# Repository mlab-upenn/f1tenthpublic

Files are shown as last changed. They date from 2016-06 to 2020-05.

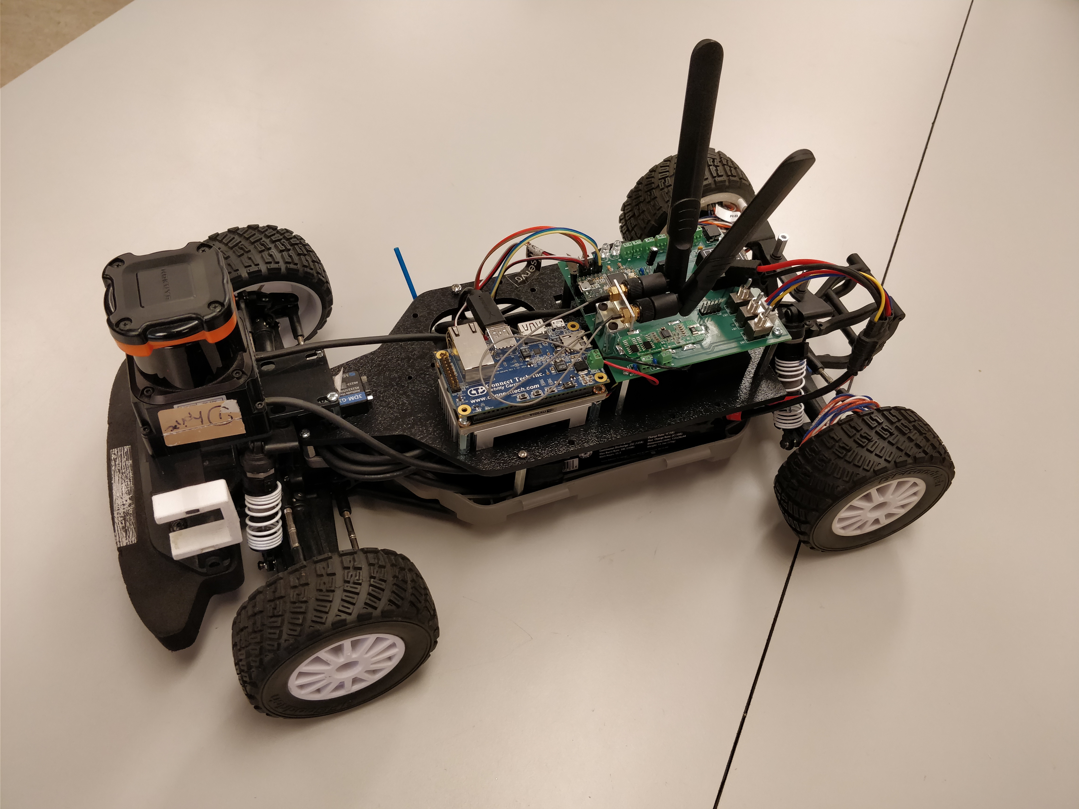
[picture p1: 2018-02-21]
images/image2.jpg

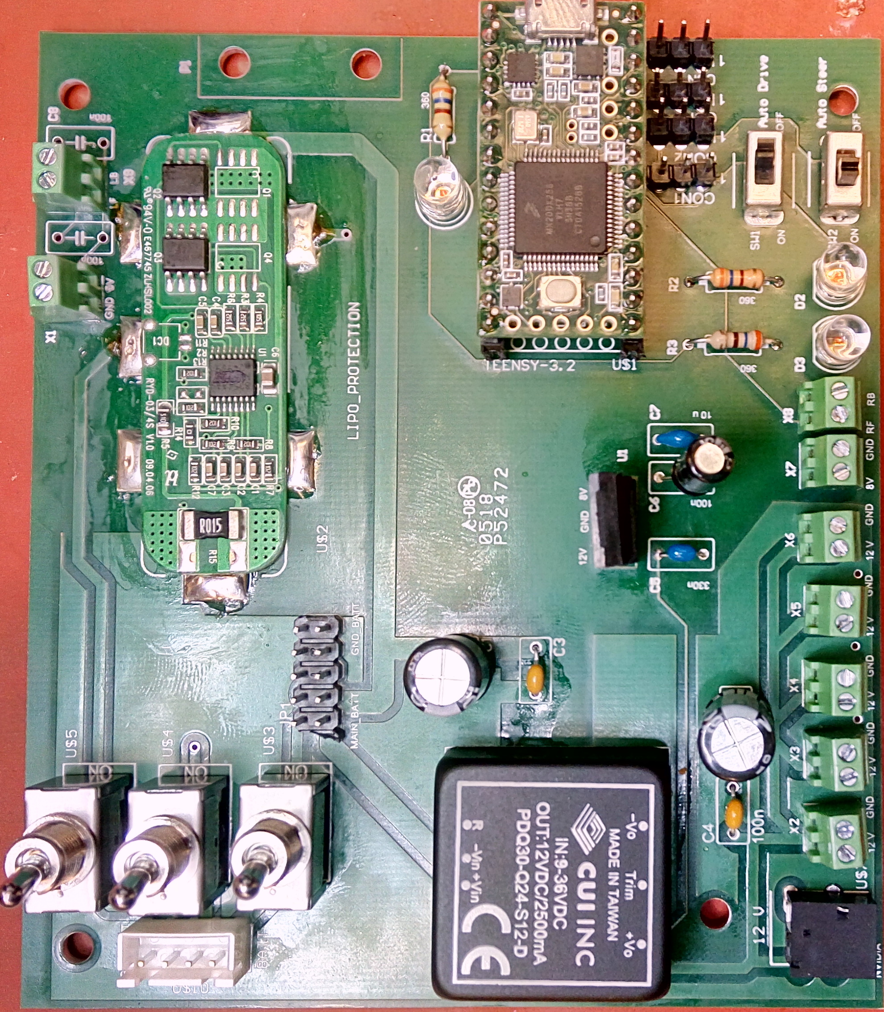
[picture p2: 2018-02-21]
images/power_board_v2.0.jpg

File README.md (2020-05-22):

# f1tenth_public, please read me
2020-05-22
This repository is no longer supported. Please see the new Build page at https://f1tenth.org/ for the most up to date BOM.

This repository hosts all of the code, CAD files, and other resources necessary to get your car ready for competition.

## F1tenth BOM 2019.xlsx
This is the bill of materials for building a F1/10 car. It contains order links for mechanical and electrical parts. The updated power board and parts list and order links are also inside.

## power-board-v3.zip
The source files of power board v3. It is designed in Altium Designer. To order the powerboard, please go to "F1tenth BOM 2019.xlsx" and find the order link in "Bill of Material for Power Board v3.0" section. The order link is https://oshpark.com/shared_projects/qvIKu3aY

### Warning: please test power board before connecting battery, Jetson and Lidar!
After soldering the power board, please test the board with a DC power supply and multimeter. 
* Using a multimeter, test if the GND_BATT pin and the opposite pin of the battery connector on the power board are shorted. Test if any 12V pin and GND pin, 8V pin and GND pin are shorted. Double check the polarity of electrolytic capacitor and the 12V to 8V DC converter. Check if the switch functions.
* Set the DC power supply to 12 V, current limit of 100 mA, and connect GND of power supply to GND_BATT pin and + of power supply to 1st pin at battery connector. Turn on power supply, and flip on the switch. Red PWR_LED should light up. Test 12V and 8V output voltage.

### Connect battery only after making sure no short circuit exists!

## Chassis
The Chassis folder contains solidworks files for making the chassis.
The following parts need to be laser cut:
* Chassis_Surfaced_MASTER_small_powerboard.DWG (for power board v3)
* Lidar_Mount_10LX.DWG or Lidar_Mount_30LX.DWG

The following parts need to be 3D printed:
* Camera_Mount.STL

The 3dPrints folder contains optional parts for zed camera.

If the FOCBOX cannot fit under the small power board, you can use only 3 standoffs to mount the power board.

## Power-board-v2.0
Old power board design source files. Obsolete. Designed in Altium Designer.

## Change log
v3:
Updated power board. Removed teensy and lithium battery charging module because no one would run the car while charging the battery.
Updated chassis to match the smaller power board.

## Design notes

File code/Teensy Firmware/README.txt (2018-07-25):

This file contains commands to setup rosserial to communicate with Teensy via ROS framework. It also involves command for generation of custom messages headers which can be accessed by code in arduino.

Setup Arduino with Teensy:

1) Setup arduino with Teensy package using link : https://www.pjrc.com/teensy/td_download.html

2) Setup rosserial : 
	Follow link : http://wiki.ros.org/rosserial_arduino/Tutorials/Arduino%20IDE%20Setup

	OR

	use commands :
	sudo apt-get install ros-indigo-rosserial-arduino
	sudo apt-get install ros-indigo-rosserial

3) To setup libraries (use custom messages):
	- go into race folder from Week 2
	- create build folder: `mkdir build`
	- move into it: `cd build`
	- run cmake on parent folder: `cmake ..`
	- now Makefile is available, so run it with: `make`
	- source created setup file: `source ./devel/setup.bash`
	- move into [place_for_arduino_projects]/libraries
	- delete old ros libs folder `rm -rf ros_lib`
	- run rosserial libraries builder `rosrun rosserial_arduino make_libraries.py .`

	Now, you should be able to find folder `race` in `ros_lib` folder with 3 header files (custom messages).

4)	Once this is configured : 
	Choose Teensy 3.2/3.1 in Tools menu of arduino software. Also make sure settings are configured to : "serial" and "96 Mhz optimized".
	After choosing the appropriate port, your arduino should be ready to dump the firmware.

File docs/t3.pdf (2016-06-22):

# Tutorial 3: The Jetson: Introduction

### The F1/10 Team

## What you should know about this board

The complete specs of the Board can be found at - Jetson Linux Homepage. (http://elinux.org/Jetson_TK1) In short, this dev board has,

- An ARM quad core Cortex-A15 CPU @ 2.3GHz
- An NVidia Kepler GK20 GPU(192 CUDA cores)
- 16GB of storage
- 2GB RAM
- Power: Takes in 12V at a current range of 1 - 5A. (Under Normal working conditions, current draw = 0.5A)
- Has optimized OpenCV libraries. Harnesses the CUDA cores for better and faster results
- The board comes up with a customised ‘Linux4Tegra’ Distribution - NVidia’s distribution of Ubuntu 14.04 with some pre-compiled binaries
There is extensive material with regard to powering on the Jetson and logging into the Desktop GUI. This NVidia (http://developer.download.nvidia.com/embedded/jetson/TK1/docs/2_GetStart/Jeston_TK1_User_Guide.pdf) guide covers the steps needed for setting up the board. There are 3 sections in that guide - ‘Setting up’ , ‘Flashing the Jetson’ and ‘Jetpack’.
We only need to go through the first section for now.
The section for ‘Flashing’ the Jetson is not required for us right now because when we boot a brand new Jetson, it already contains the Linux4Tegra files and an install script.
For developer tools related to CUDA and cross compiling resources, users can follow the 3rd section that talks about the Jetpack.
Once you switch on the Jetson, you should upgrade the kernel to ‘The Grinch Kernel’. This will enable important features needed for the race car.
Follow http://jetsonhacks.com/2015/05/26/install-grinch-kernel-for-l4t-21-3-on-nvidia-jetson-tk1/

## References

- Jetson Wiki (http://elinux.org/Jetson_TK1)
- JetsonHacks Blog Post (http://jetsonhacks.com/) (Its really good)
- NVidia Forums (https://devtalk.nvidia.com/default/board/162/)
- A Setting up Jetson Video (https://www.youtube.com/watch?v=ghqM8pzJZxg)
- Nvidia Page (https://developer.nvidia.com/embedded/jetson-development-pack)

1

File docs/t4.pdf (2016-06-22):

# Tutorial 4: Setting Up the Wireless Network

### The F1/10 Team

## Introduction

This tutorial covers the configurations required to be made on the Jetson and laptop in order to setup the point to point wireless connection between them using ubiquiti pico station.

## Setting up the Jetson’s ethernet:

Connect the Jetson to display via HDMI port. Also make sure you have a USB mouse and Keyboard connected to it.

### Physically connect the Jetson to PicoStation 2HP

- Plug in the POE (power over ethernet) injector
- Plug the PicoStation into the POE port
- Connect this system into Jetson’s LAN port

### Configure the Jetson for a static IP on the 192.168.1.x subnet

- Open network connections on Jetson
- Go to the ”wired” tab
- Edit the ethernet connection
- Go to the ”IPv4” Settings tab
- Edit the settings as follows:
– Method: Manual
– Address: 192.168.1.x (x = anynumber) (The video tutorials in further lectures will use: 192.168.1.1 to connect to Jetson via SSH. Make sure you remember the value of x you set here while following future videos.
– Netmask : 255.255.255.0
– Gateway : 192.168.1.x
– Save –> Close
- The network should say connected, you might need to select ’wired connection 1’ from the wireless toolbar and/or unplug and replug the wires

## Configuring the PicoStation

You must still be connected to the PicoStation via an ethernet connection or the PicoStation’s previously setup network (if there is one) before continuing.

### Connecting to the Pico Station

- Open a web browser and access the PicoStation’s IP address – Default IP address is 192.168.1.20
– enter http://[IP address]

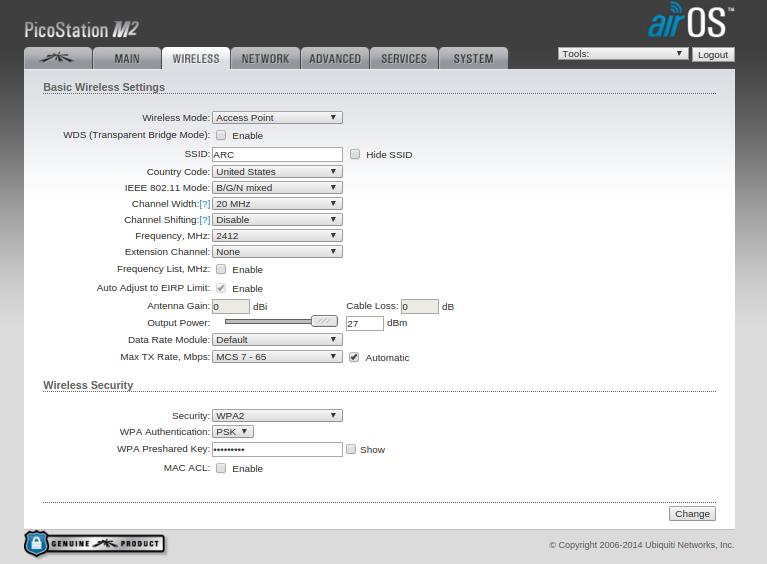
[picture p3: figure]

– Note: IP address can be changed
- Enter username and password when prompted – Default username: ubnt
– Default password: ubnt
– Note: Username and password can be changed

### Configuring the PicoStation

- Go to the ”WIRELESS” tab
- Change the settings to the following: – Wireless Mode: Access Point – SSID: [desired SSID]
* example: My network
– Country Code: United States
– IEEE 208.11 Mode: B/G/N mixed – Channel Spectrum Width: 20 MHz – Channel Shifting: Disabled
– Channel: 1-2412 MHz
– Output Power: no greater than 27 dBm (U.S. regulation) – Data Rate Module: Default
– Security: WPA2
– WPA Authentication : PSK
– WPA Preshared Key : Your Password

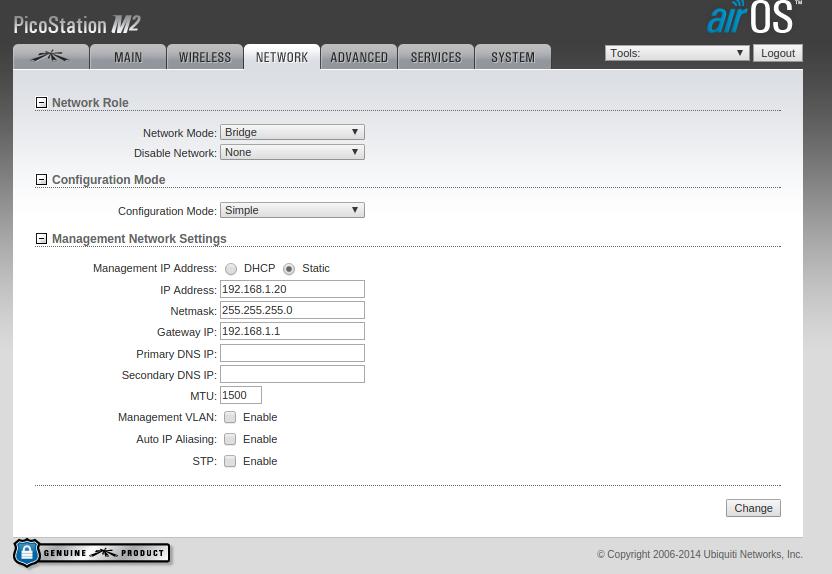
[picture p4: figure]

- Go to the ”NETWORK” tab
- Change the settings to the following: – Network Mode: Bridge
– Disable Network: None
– Bridge IP Address: Static – IP Address: 192.168.1.20 – Netmask: 255.255.255.0
– Gateway IP: 192.168.1.1
– Change –> Apply

## Setting up the Remote System’s Wireless

### Setting up the wireless

- Go back to your Network Connections
- Go to the ”Wireless” tab
- Add a new wireless connection
– Name it after the intended robot
– Give it the same SSID that you gave the PicoStation – Go to ”IPv4 Settings” tab
– Change the settings as follows:
* Method: Manual
* Address: 192.168.1.x (x=any number, 110 in our case for future examples) * Netmask: 255.255.255.0
* Gateway: 192.168.1.x (x=any number, 110 in our case)

– Save –> Close

### Connecting via SSH

Now once you are connected to the wireless network, you can ssh into the Jetson from your remote system’s terminal, using following command:

ssh ubuntu@192 . 1 6 8 . 1 . 1

Here ”ubuntu” is the username setup in Jetson and the ip shown is the IP configured in the first step in setting up of pico station.

## Establishing ROS over network

In order to let ROS communicate directly between you Jetson and remote system, and send messages to and fro, it requires a few minor configurations. While operating Jetson via remote system, you might need to see the data published over certain topics by scripts running on Jetson. You might need to visualize the location of the car, or the LiDAR scans or maybe the map of the surrounding. A GUI called Rviz allows this visuals but we cannot install that on Jetson. Establishing ROS to communicate over the network, will allow us to use this GUI to visualize data in this way. We will cover this visualization in the next tutorial.
To set this up, follow the steps below:
- On the terminal of remote system, when present working directory is the home folder, open ”.bashrc” using any text editor.
- Add the lines :

export ROS_MASTER_URI=http ://192.168.1.1:11311 export ROS_IP=192.168.1.110

- Whenever you want to revert this, replace it back by :

export ROS_HOSTNAME=localhost
export ROS_MASTER_URI=http :// localhost :11311
- Open the hosts file under path : /etc/, and add the line :

192.168.1.1 ubuntu

Here it is assumed that the ”ubuntu” is the account username in Jetson, and 192.168.1.1 is the IP address to which the wireless was setup on Jetson.

Now on the Jetson Side:
- Open the file .bashrc from home folder.
- Add the following line when you want to transfer data to remote system over network

export ROS_IP=192.168.1.1

- To revert it back to original settings, replace above line with :

export ROS_HOSTNAME=localhost
export ROS_MASTER_URI=http :// localhost :11311

- Now navigate to the ”/etc/hosts” file and add the following line to it: (The username refers to the username of your laptop. And the IP mentioned corresponding to the IP you used while setting up the remote system/laptop’s wireless.

192.168.1.110 username

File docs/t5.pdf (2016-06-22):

# Tutorial 5: Sensor Configuration and Rosbags

### The F1/10 Team

## Introduction

This tutorial will cover the installation of various packages and settings to be configured to get the LiDAR and Inertial Measurement Unit working on Jetson. At the end we will go through few commands that can be used to record the data to run them later on for simulations.

## Transcript to the Video Tutorial

In this video we will install and configure the Hokuyu LiDAR and Razor IMU. Luckily both have of these have ROS packages readily available and hence the process is quite straight forward. For any other sensor you might want to use in future, you can look up to its package availability in ROS and follow similar steps.

Connect your jetson board to display, keyboard, mouse and an ethernet cable.

On the terminal use the following command to install the Hokuyu node package:

sudo apt−get i n s t a l l ros−indigo−hokuyu−node

When you connect your lidar to jetson, it generally connects to ACM ports which can be checked using the command :

l s /dev/ttyACM*

This will list all the ACM ports currently being used. If you are doing this first time, you need to provide specific permissions to the port by using the command :

sudo chmod a+rw /dev/ttyACM_

This will provide read write permissions for ROS to communicate with the sensor. Now, to check the data coming from LiDAR, as explained in the initial ROS tutorials, run the roscore. On the other terminal , run -rostopic list. This will show all the topics currently being published.

The scan topic is the one we are interested in.

rostopic echo /scan

These dump of messsages might not make sense now, but these values correspond to the distance sensed by LiDAR at different angles.

We can visualize these laser scans by a GUI interface called Rviz. Unfortunately due to the driver issues Rviz doesn’t work on Jetson. If you had setup ROS over Network explained in previous tutorial properly, you can run Rviz over your system that has been setup for the network.

AS you can see these are the laser scans. It might not show up on its own on your system. Insert it using the add button visible here.

Now to install the packages for IMU, go back to Jetson and install the package using command :

sudo apt−get i n s t a l l ros−indigo−razor−imu−9dof

Lets keep the default parameters untouched, and take a copy for us to make some tweaks

roscd razor_imu_9dof/ config cp razor . yaml my_razor . yaml

You can calibrate the IMU by following the link provided in the reference. and mention the measured offset values in the newly made file. To confirm the communication of IMU with ROS interface use the launch file:

roslaunch razor_imu_9dof razor−pub . launch

You can now run ”rostopic list” in another window and look for the /imu topic. ”rostopic echo /imu” will allow you to see the incoming data stream. So the packages for both these sensors are ready. You can follow similar steps to install it on any ROS system. Its better not to clog Jetson’s memory with useless packages and hence you install any extra packages on your laptop.

For example to visualize the IMU data, you need to install the python-visual package. Install the IMU packages on your ROS system as well. Then install the python- visual using :

sudo apt−get i n s t a l l python−visual

Once done, run the launch file :

roslaunch razor_imu_9dof razor−pub−and−display . launch

The red board is following the motion of my IMU. Feel free to change the config parameters and play around with this to improve the performance.

## Introduction to Rosbags

This tutorial covers data logging tools provided by the Robot Operating System. These tools allow users to capture data from various sensors and then play it back offline. This tutorial goes over some basic commands to utilise these logging tools. This should be ideally read after you go through the Sensor Integration Video.

## Rosbags: Tutorial 5.1

In this tutorial we are going to learn about rosbags. You would now know how dependant we are on the various sensors for testing and running our algorithms. The problem arises when we don’t always have access to these sensors. rosbag is the tool provided by ROS that lets us log sensor data and play it back as per our need.
It stores this sensor data as the topics on which it was published and when the data is played back, its published again on those same topics. Therefore the remaining part of our system need not change when we need to test anything ofline.

You could go ahead and download the files located at https://github.com/mlab-upenn/f1_10_code_public/
- Git Repo

In a terminal after initialising roscore run this command,

$ rosbag play lidarBag . bag − −clock

This .bag file contains the data from our LIDAR. After this command, on another terminal, use rostopic list to verify that you are able to see the /scan topic. This is the topic that the LIDAR was publishing on when it was actually used. The clock arguement here is a very important paramter. It provides a simulated ‘clock’ for the ROS network. The data playing back from the bags would have time stamps highly offset from the current time. This discrepency in time between the incoming data and the rest of the system often leads to unpredictable and generally unwanted behaviour. For this reason, the ’clock’ is used - It provides all the ROS systems with a common time stamp - a simulated time stamp. If you perform a rostopic list in a terminal, you will see the /clock topic that is being published. The other subsystems of your ROS framework need to be told that they must follow the simulated time and not actual time. To do this we must set the ros parameter use_sim_time to true. To do this, run the following command on a terminal

$ rosparam set use_sim_time

To check the value of the paramter use,

$ rosparam get use_sim_time

Ensure this configuration of use_sim_time every time you playback a bag.
Now we will go through the process of actually taking recording a bag. Lets use the Hokuyo and the IMU as our sensors. Launch the sensors using,

$ rosrun hokuyo_node hokuyo_node $ roslaunch razor imu_launch

For bagging all current topics, use the -a command line argument with the command

$ rosbag record −a

You can choose to terminate the bagging process at any time by simply killing that process - Ctrl + C should do it.
You will notice now that you will have a bag in your current folder. Use

$ rosbag <bag name>.bag info

to view the contents of the bag. This data can be then played with the command shown earlier to simulate the LIDAR data ofline.
Hopefully you guys understood the need and usefullness of the bagging process. This tutorial like the others was a very concise version of the Official tutorials on the ROS Wiki. Please visit [1] for more commands and options regarding the rosbag tool.

## References

[1] http://wiki.ros.org/rosbag - Rosbags Wiki
[2] Calibrating the Inertial Measurement Unit : Section 7 in http://wiki.ros.org/razor_imu_9dof

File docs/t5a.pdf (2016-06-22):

# Extras: Configuring the Hokuyo UST 10LX

### The F1/10 Team

## Introduction

This tutorial covers setting up the UST 10LX LIDAR in regard to its network configuration. (You will need access to a windows system with administrator rights for completing this tutorial)

## LIDAR Setup

The LIDAR communicates with the jetson through the Ethernet to USB converter and this connection shows up on the Jetson as a new ethernet connection. Use ‘ifconfig’ in the terminal to verify this.

$ i f c o n c f i g

There are now two ethernet connections on the Jetson - one for the ubiquiti and the other for the LIDAR. To make sure we can communicate between these two we have to ensure that they are on the same subnet. Lets start with the default values of the IP for the LIDAR. View the datasheet for the particulars [1].
For this particular tutorial the following ip addresses are used

# gateway of ubiquti network − 192.168.1.1

# eth1 ( ubiquiti network ) on jetson − 192.168.1.5

# eth2 (LIDAR connection ) on jetson − 192.168.0.10 − Default values

- STEP 1: Lets first manually assign the correct IP address to the LIDAR. On the windows system download the URG data viewing tool and the IP changing tool - [2], [3].
Manually assign an ip address to the ethernet network connection of the Windows PC with these values:

IP Address 192.168.0.15
Subnet Mask 255.255.255.0
Default Gateway 192.168.0.1

Once you donwload these tools, connect the LIDAR to the Windows machine - Use the Benri data viewing tool to verify that your machine has detected the LIDAR and that you can see the data(Fig. 1).

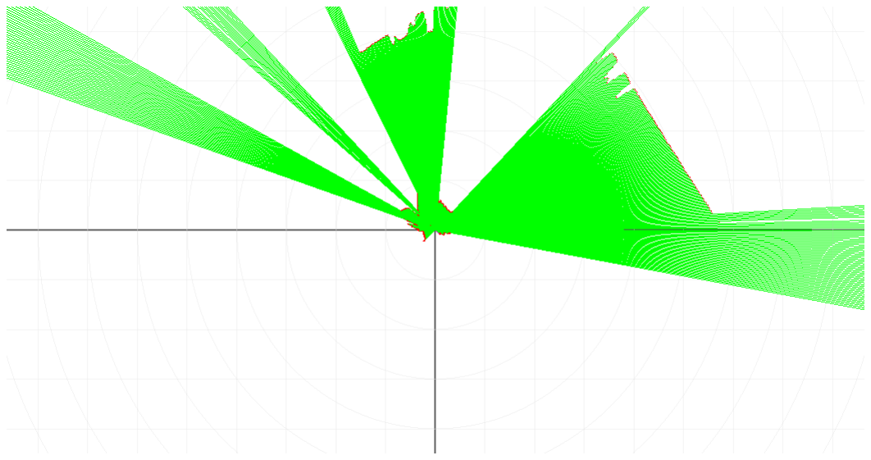
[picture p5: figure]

Figure 1: Data as seen on the UrgBenri Data viewing tool

Now, use the ip changing tool to assign the following values to the LIDAR.

IP Address 192.168.1.11
Subnet Mask 255.255.255.0
Gateway 192.168.1.1

Once the dialog box says the ip is ‘Updated’, disconnect the device from the machine. Change the ethernet ip of the

machine to

IP Address 192.168.1.15
Subnet Mask 255.255.255.0
Default Gateway 192.168.1.1

Plug in the LIDAR back into the system and make sure you can see visualize the data on the URGBenri tool.
- STEP 2: We will now configure the network setup on the Jetson. Create a new ethernet connection in linux4Tegra[4] with these values

Connection Name: Hokuyo
IP Address 192.168.1.15
Subnet Mask 255.255.255.0
Default Gateway 192.168.1.1

Once you make this new connection, you should be able to plug in the LIDAR and the ubiquiti and be able to connect to both these devices, i.e, ‘ifconfig’ should display two ethernet connections - eth0 and eth1 with the correct IPs’ for each. (If you were connected to the ubiquiti network through your own systems, you might notice that you get disconnected from the network the moment you connect the LIDAR to the Jetson. We will address this issue in the next step)
- STEP 3: We will now setup a bridge network that allows the 2 ethernet connections on the Jetson to coexist. First, install bridge-utils on the Jetson.

$ sudo apt−get i n s t a l l bridge−u t i l s

Once installed follow the enter the listed commands into the terminal(on the Jetson)

1. sudo brctl addbr br0
2. sudo brctl addif br0 eth1
3. sudo brctl addif br0 eth2
4. sudo i f c o n f i g br0 192.168.1.2 netmask 255.255.255.0 up

(*Note: make sure you already don’t have some existing connection on 192.168.1.2 - If thats the case, just set the bridge network to any other available IP on 192.168.1.xx) After this step, you should be able to see br0 listed as a connection under when you do ifconfig.
- STEP 4: You should now be able to connect back to the ubiquiti network from your systems. Use nmap[5] to see the different devices connected on your network. In the terminal, type

$ nmap −sP 192.168.1.0/24

You should be able to view the host names with the IPs of all the devices sharing your network. You must be able to spot the LIDAR and the Jetson as separate devices on this list.
- STEP 5: Once you see the devices listed with nmap, you should be able to ssh into the Jetson and run

$ rosrun urg_node urg_node _ip_address :=192.168.1.11

(Note: You should have the urg node package installed when you need to run this node)

$ sudo apt−get i n s t a l l ros−indigo−urg−node

This should start broadcasting the /scan topic. From your personal computer, make sure you can echo this topic. You are all set now to use the LIDAR over network.

## References

[1] UST 10LX datasheet (http://en.manu-systems.com/ust-10lx_spec_E.pdf)

[2] URG DataViewing Tools (https://www.hokuyo-aut.jp/02sensor/07scanner/download/data/UrgBenri.htm)
[3] URG IP changing tool (https://www.hokuyo-aut.jp/02sensor/07scanner/download/data/Urg_ip_changer_utm_en.zip)
[4] Create new ethernet connection (https://help.ubuntu.com/16.04/ubuntu-help/net-manual.html)
[5] nmap Tool (https://nmap.org/)

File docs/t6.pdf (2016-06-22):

# Tutorial 6: Distance finder and PID

### The F1/10 Team

## Introduction

This article contains the transcript of the week 2 Video Tutorial 6: Distance finder and PID. The aim of this tutorial is to give a brief explanation of simple algorithm to maintain the car parallel in a corridor. It involves how to use the sensor data from lidar and how to formulate a controller for the same.

## Transcript of Video Tutorial

In this tutorial we will learn how to make our car run parallel to a wall at a fixed distance. We will implement two nodes, a node that uses the laser scans from the lidar to determine the distance from the wall and an other node to apply pid on this error to determine the steering angle. We shall follow the algorithm described in the lectures.
Lets go through a simple procedure to calculate the distance of the wall from the car and hence calculate the deviation from the desired trajectory. The lidar scans from right to left corresponding to 0 to 180 degree with 90 degree being the front of the car. We pick 2 rays at 0 degree and theta degree, theta being some angle between 0 to 70 degree.

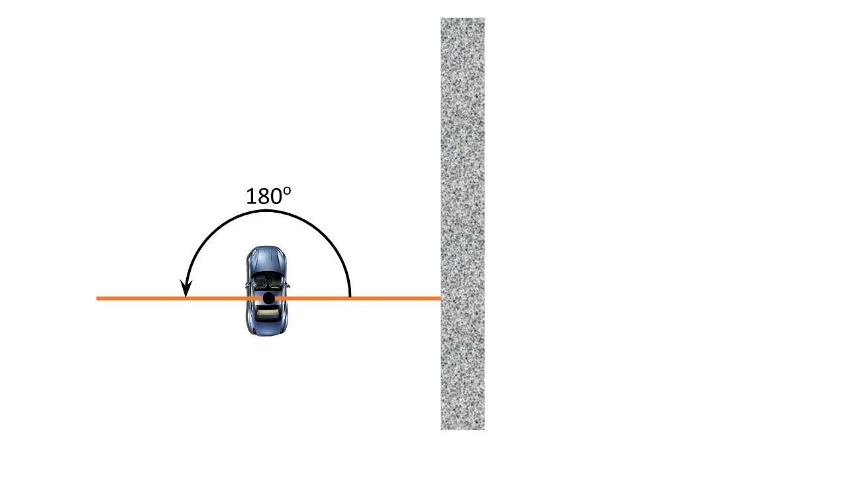
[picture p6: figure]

Figure 1: Lidar scan angles

Let alpha be the orientation of the car with respect to the wall. By solving the geometric problem we can establish alpha as tan inverse of a cos(theta) - b/asin(theta), and AB as b cos(alpha).

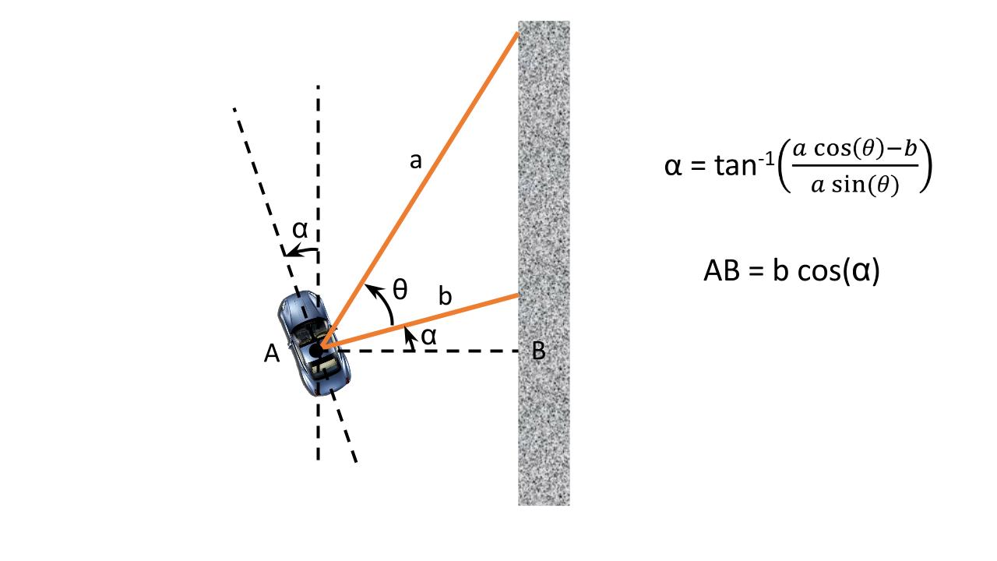
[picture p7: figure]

Figure 2: Calculating the orientation and distance from the wall

1

If the desired trajectory is 1m from the wall then generally the error that has to controlled by the PID is 1
- AB.
But we cannot use this distance directly. Due to the high speed of the car and a finite delay in execution of the manoeuvre we project the car forward certain distance from its current position. Hence now the distance of the car from the wall becomes AB + AC*sin(alpha)
Hence the error to be compensated for is the difference between CD and the desired trajectory.
Now we have the error, we can use it in the PID equation to determine the amount of correction to be given to the steering.

Figure 3: Projecting the car future in time

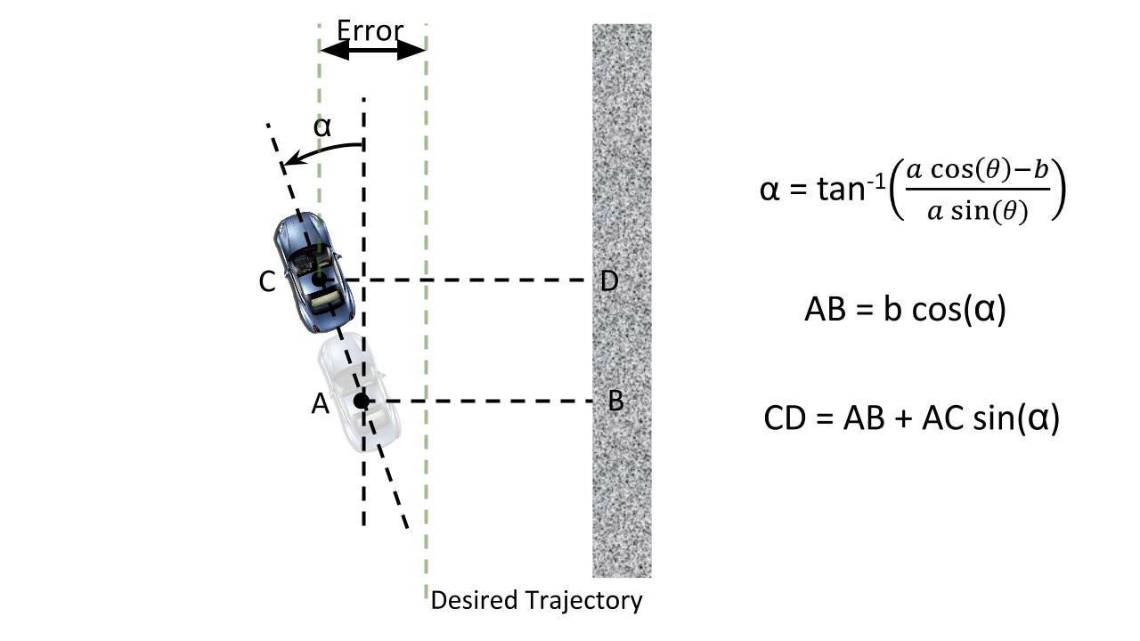
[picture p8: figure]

We use the standard PID[1] equation, where e(t) is the error from the desired trajectory. As seen in the lecture we will be using only Kp and Kd controls.
Hence we implement this as a tunable variable Kp times error plus another tunable variable Kd times the difference in error.

Vθ = Kp × e(t) + Kd

de(t)
dt
Vθ = Kp × error + Kd × previous error - current error

Use this value to increment or decrement your your steering angle. In the practice session you will be implementing this in code.

## References

[1] A simple PID tutorial (http://www.csimn.com/CSI_pages/PIDforDummies.html)

2

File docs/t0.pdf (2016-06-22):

# Tutorial 0: The Robot Operating System

### The F1/10 Team

## Installing ROS Indigo on Ubuntu 14.04

This tutorial assumes that the host OS on which ROS Indigo is to be installed is Ubuntu 14.04 LTS. This tutorial offers a very concise walkthrough of the ROS Installation. For a detailed step-by-step explaination of the commands used, please visit the ROS Inidgo Installation page . (http://wiki.ros.org/indigo/Installation/Ubuntu)
If you have the Trusty 14.04.2(use lsb_release -a in the terminal to find out) distribution, you might face dependancy issues for which it is recommended you vist the link above before begginig the install. The steps listed below install the ‘Desktop-Full’ ROS Indigo. This means that simluators like Gazebo, rViz along with a large number of ROS packages are installted as well. If your host machine has any constraints regarding memory you should visit the link above to install a trimmed version of ROS Indigo.
Again, this is a very brief guide and if there is any problem at any step please visit the link above.
Execute the following commands/steps in the terminal one after the other.
- Configre Ubuntu repositories to allow for ‘multiverse’, ‘universe’ and ‘restricted’. (How to : Configure Repositories) (https://help.ubuntu.com/community/Repositories/Ubuntu)
- sudo sh -c ‘echo “deb http://packages.ros.org/ros/ubuntu $(lsb_release -sc) main” > /etc/opt/sources.list.d/ros-latestlist’
- sudo apt-key adv –keyserver hkp://pool.sks-keyservers.net –recv-key 0xB01FA116
- sudo apt-get update
- sudo apt-get install ros-indigo-desktop-full
- sudo rosdep init
- rosdep update
- echo “source /opt/ros/indigo/setup.bash” >> ∼/.bashrc
- source ∼/.bashrc
- sudo apt-get install python-rosinstall
You should now have ROS Indigo on your system.

## References

- ROS Indigo Installation (http://wiki.ros.org/indigo/Installation/Ubuntu)

1

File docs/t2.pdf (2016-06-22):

# Tutorial 2: The Robot Operating System: Basics 2

### The F1/10 Team

## Introduction

This article contains the transcript of the Video Tutorial 2: The Basics of ROS (Part 2). This tutorial is based on tutorial 12 covered by the official ROS tutorials[1]. The aim of this tutorial is to familiarize you with the framework of the Robot Operating System by implementing your own simple publisher and subscriber nodes in python.

## Transcript of Video Tutorial

In this tutorial lets write our own publisher node that publishes a string hello world and a subscriber node that receives the string. We begin by creating a workspace. In your root folder, execute these commands:

$ mkdir −p ~/catkin_ws/ src $ cd ~/catkin_ws/ src
$ catkin_init_workspace

Catkin[2] is a ROS tool for compiling the different subsystems and modules used in ROS. Its like CMake, but over a larger scale and its specially designed keeping in mind some ROS requirements. Perform a catkin_make from the root of the workspace.

$ cd . .
$ catkin_make

The devel and build folders at the root of the workspace are where the linked libraries and the complied code in machine language resides. Source the environment using

$ source devel/setup . bash

We will now create a package. In the src folder,type in the command

$ catkin_create_pkg beginner_tutorials std_msgs rospy roscpp

The beginner_tutorials is the name of the package and the std_msgs, rospy, roscpp are dependencies that we are defining. Use catkin_make from the root of the workspace. Source and confirm if your workspace is indeed added to your current environment by doing

$ echo ROS_PACKAGE_PATH

We will now use the roscd command to access a package within a workspace. If the environment containing the package is sourced, we should be able to naviagte to the pacakge by using roscd package name. here we can verify this by using

$ roscd beginner t u t o r i a l s

We will create a new folder to hold all our code

$ mkdir s c r i p t s
$ cd s c r i p t s

Place the talker.py and listener.py files in the script folder just created.
Lets walk through the talker.py file first
- ‘from std_msgs.msg import String’ line imports the string data type from the std_msgs library that we included during the creation of beginner_tutorials package
- The rospy.Publisher function creates a new topic called chatter of type string
- rospy.init_node initializes the node called talker, and
- pub.publish(hello_str) publishes the string containing hello world with the system time. The listener.py consists of a similar structure.
- Like in the talker node rospy.init_node intializes the listener node.
- But this node subscribes to the chatter topic published by the talker node using the rospy.Subscriber function
- The callback function is an interrupt function that is called every time some data is published to the chatter topic. Here we just print back the string that it received.
Before we can run the nodes we need to give executable permissions to these files using

$ sudo chmod +x talker . py l i s t e n e r . py

To build the nodes navigate to the root of the workspace and run

$ cd ~/catkin_ws
$ catkin_make

make sure the process ends without errors Start roscore,

$ roscore

then in new terminals run the talker.py and listener.py nodes. Make sure you source the workspace using

$ source ~/catkin_ws/devel/setup . bash

every time you open a new terminal. Run the nodes using

$ rosrun beginner_tutorials l i s t e n e r . py

and in a seperate terminal

$ source ~/catkin_ws/devel/setup . bash $ rosrun beginner_tutorials talker . py

Go ahead and run all the rosnode, rostopic, rosmsg and rqt_graph commands to analyze the program. In the next tutorial you will learn how to configure and run ROS on the jetson.

## References

[1] ROS Beginner Tutorial 12 (http://wiki.ros.org/ROS/Tutorials/WritingPublisherSubscriber%28python%29)
[2] What exactly is catkin (http://wiki.ros.org/catkin)

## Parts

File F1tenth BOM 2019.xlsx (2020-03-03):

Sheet: v3.0
Component | Quantity | Cost |  | Link | Order Status | Comment
Traxxas 1/10th Car platform with RC, NiMH battery 3000mAh, 7 cell and Charger | 1 | $299.95 | $299.95 | http://www.jegs.com/i/Traxxas/430/74054-6/10002/-1 | 0 | If out of stock, see alternate platforms below
USB wifi dongle |  | $8.99 | $0.00 | http://amzn.to/2nQGg3Z | 0 | use onboard WLAN or usb dongles like these instead of Ubiquity picostation ( product is discontinued)
Li-Po battery 5000mAh, 3 cell 11.1V #2872 | 1 | $74.99 | $74.99 | https://traxxas.com/products/parts/batteries/idpowercellbatteries/lipo/2872X-5000mah-111v-3S-25C | 0 | Combinations also available for purchase : https://www.amazon.com/dp/B01M0PKSGB https://www.amazon.com/Traxxas-Maxx-Brushless-BATTERY-CHARGER/dp/B00ERUAQYO
 |  |  |  | https://www.amazon.com/Traxxas-2831X-5000mAh-3-Cell-Battery/dp/B01A6YDKS8
Li-Po battery Charger #2970 | 1 | $49.99 | $49.99 | https://traxxas.com/products/parts/chargers/2970ezpeakplus4ampid https://www.amazon.com/Traxxas-2970-EZ-Peak-Charger-Identification/dp/B00OAFYLJC https://traxxas.com/products/parts/chargers/ezpeak-dual-8amp-id | 0
Nvidia Jetson TX1 | 1 | $299.00 | $299.00 | https://www.nvidia.com/en-us/autonomous-machines/embedded-systems-dev-kits-modules/ http://www.nvidia.com/object/edu-discount.html http://www.nvidia.com/object/jetsontx2-edu-discount.html | 0 | Avail Tx1/TX2 Development Kit through Academic discount Also, either of TX1 or TX2 can be used
Orbitty Carrier board for TX1 | 1 | $173.00 | $173.00 | http://connecttech.com/product/orbitty-carrier-for-nvidia-jetson-tx2-tx1/ | 0 | works for both TX1 or TX2
USB Hub | 1 | $29.95 | $29.95 | https://www.amazon.com/AmazonBasics-Port-USB-Power-Adapter/dp/B00DQFGH80 https://www.amazon.com/Sabrent-4-Port-Individual-Switches-HB-UM43/dp/B00JX1ZS5O | 0
FTDI | 1 | $15.00 | $15.00 | https://www.sparkfun.com/products/9873 | 0 | optional - depending on the IMU module
Sensors
SparkFun 9DoF Razor IMU M0 | 1 | $49.95 | $49.95 | https://www.sparkfun.com/products/14001 | 0
3DM Microstrain IMU (optional) |  |  |  | http://www.microstrain.com/inertial/3dm-gx3-25 |  | use either IMU
UM7 IMU (optional) |  |  |  | https://www.pololu.com/product/2740 http://www.chrobotics.com/shop/um7-orientation-sensor
LIDAR | 1 | $1775.00 | $1775.00 | https://acroname.com/products/HOKUYO-UST-10LX-LASER?sku=R359-UST-10LX | 0 | or scan-sweep lidar
Structure Sensor (Optional) | 1 | $379.00 | $379.00 | https://store.structure.io/store | 0 | or sviz - lidar and camera bundle
Asus xtion pro (optional) |  | - | - | https://www.amazon.com/Asus-Xtion-PRO-LIVE-90IW0122-B01UA/dp/B00CET0ZBO https://www.newegg.com/Product/Product.aspx?Item=N82E16826785030 |  | out of stock mostly
ZED Camera (Optional) |  | $449.00 | $0.00 | https://www.stereolabs.com/ | 0 | or rgb option
Mechanical
Traxxas 3769 Spring Preload Spacers | 2 | $5.22 | $10.44 | http://amzn.to/2aazUF7 | 0
Allen Key Set | 1 | $8.99 | $8.99 | http://amzn.to/29PazD5 | 0
Camera mount - 3d printed | 2 |  |  | - |  | 3d printed from files provided
Ubiquity Picostation mount - 3d printed ( optional) | 1 |  |  | - |  | 3d printed from files provided
plastic spacers /standoffs | 4 |  |  |  |  | between the carrier board and the TX1 mounting
3mm ABS | 1 | $6.38 | $6.38 | http://amzn.to/29E6CTy https://www.mcmaster.com/#8586k361/=1bnvvd6 | 0 | For Lidar mount of chassis
6mm ABS | 1 | $9.74 | $9.74 | http://amzn.to/29PayPj https://www.mcmaster.com/#8586k371/=1bnvv5e | 0 | For Base plate of chassis
6mm Hex M/F Standoff 14mm | 8 | 4.2 | $33.60 | https://www.mcmaster.com/#93655a425/=1bhcvt6
6mm Hex F/F Standoff 19mm | 6 | 2.79 | $16.74 | https://www.mcmaster.com/#92080a430/=1ak2153
6mm Hex F/F Standoff 45 mm | 4 | 2.8 | $11.20 | https://www.mcmaster.com/#92080a030/=1ak1644
6mm Hex F/F Standoff 35 mm | 4 | 2.53 | $10.12 | https://www.mcmaster.com/#92080a024/=1ak1tj1
M3 screws x 10 mm | 26 | 7.01 | $7.01 | https://www.mcmaster.com/#91290a115/=1bhcq40 |  | for a pack of 100
M3 screws x 20 mm | 6 | 6.85 | $6.85 | https://www.mcmaster.com/#91502a109/=1bhcs7r |  | for a pack of 50
Power Board
Refer to the Power Board BOM for specific components
Miscelleneous
Traxxas 2976 AC to DC Converter | 1 | $25.79 | $25.79 | http://amzn.to/29Fx5xq | 0
Micro USB Cable | 1 | $4.99 | $4.99 | http://amzn.to/29xNHFc | 0 | for teensy to usb hub
Ethernet cable (optional) | 1 | $2.99 | $2.99 | http://amzn.to/29xO2ry | 0 | for ubiquity (optional)
POE cable (optional) | 1 | $3.99 | $3.99 | http://amzn.to/29D7Lou | 0 | for ubiquity (optional)
Traxxas Lipo to JST balance cable extender | 1 | $14.99 | $14.99 | https://www.amazon.com/HobbyStar-Traxxas-Charge-Adapter-Adapters/dp/B076N68H4G https://www.amazon.com/dp/B071GS515J/ref=psdc_2234135011_t1_B075W3C42B
USB to Ethernet adapter ( for lidar with ethernet conn) | 1 | $9.49 | $9.49 | https://www.amazon.com/Cable-Matters-Ethernet-Network-Adapter/dp/B00ET4KHJ2
Servo cable | 1 | $3.00 | $3.00 | http://amzn.to/29xPaeq | 0 | ($3.06 per pack of 10)
4 AA batteries | 1 | $7.18 | $7.18 | http://amzn.to/29EIImY | 0 | for RC
SD Cards (optional) | 2 | $24.95 | $49.90 | http://amzn.to/29ItJe7 | 0
Bill of Material for Power Board v4.0
Revised by Kim Luong (kimluong@seas.upenn.edu) 2019-09-05 10:47AM EST
Comment | Quantity | Cost |  | Components |  | Comment | Order Link | Comments | Digikey Part Number
Power Board | 1 | $30.00 | $30.00 |  |  | Comes in packs of 3 | https://tinyurl.com/f110powerboard2019
560 ohm | 1 | $0.04 | $0.04 | R1 |  | Resistor |  | Any resistor around 500 ohm should work | ‎CF14JT560RCT-ND‎ (https://www.digikey.com/product-detail/en/CF14JT560R/CF14JT560RCT-ND/1830344/?itemSeq=302805132)
0.33uF | 1 | $0.45 | $0.45 | C5 |  | CAPACITOR, American symbol |  |  | ‎445-181227-1-ND‎ (https://www.digikey.com/product-detail/en/FG16X7R2A334KNT06/445-181227-1-ND/9740707/?itemSeq=302805131)
0.1uF | 3 | $0.23 | $0.69 | C6, C3, C4 |  | CAPACITOR, American symbol |  |  | BC1084CT-ND
100uF | 2 | $0.31 | $0.62 | C1, C2 |  | CAPACITOR, American symbol |  |  | ‎P5182-ND‎ (https://www.digikey.com/product-detail/en/ECA-1HM101/P5182-ND/245041/?itemSeq=302805123)
10uF | 1 | $0.23 | $0.23 | C7 |  | CAPACITOR, American symbol |  |  | 493-5915-1-ND‎ (https://www.digikey.com/product-detail/en/UVR1H100MDD1TD/493-5915-1-ND/3438479/?itemSeq=302805129)
12V to 8V LDO | 1 | $0.86 | $0.86 | U1 |  | 12V to 8V LDO |  |  | BA7808CP-E2CT-ND‎ (https://www.digikey.com/product-detail/en/BA7808CP-E2/BA7808CP-E2CT-ND/2357332/?itemSeq=302805130)
12V_TRANSFORMER | 1 | $34.94 | $34.94 | U$9 |  | CUI Inc ?? SERIES: PDQ30-D ?? DESCRIPTION: DC-DC CONVERTER http://www.mouser.com/pdfdocs/pdq30-d.pdf |  |  | ‎102-3892-ND‎ (https://www.digikey.com/product-detail/en/PDQ30-Q24-S12-D/102-3892-ND/6165425/?itemSeq=302805124)
2 Pin Terminal Blocks | 7 | $0.91 | $6.37 | X1, X2, X3, X4, X5, X6, X7 |  | .100 (2.54mm) Center Header - 2 Pin" |  |  | ‎ED10561-ND‎ (https://www.digikey.com/product-detail/en/OSTVN02A150/ED10561-ND/1588862/?itemSeq=302805120)
Toggle Switch | 1 | $4.51 | $4.51 | U$3 |  | SPST two lead switch Pin 2 is common Swtich Closed on Down Position DigiKey: http://www.digikey.com/product-detail/en/nkk-switches/M2011S2A1W01/360-3240-ND/1049342 Data Sheet: http://2t70un3m1d9z1kztamkdrd38.wpengine.netdna-cdn.com/wp-content/uploads/2016/02/MtogglesBushing.pdf |  |  | ‎360-3240-ND‎ (https://www.digikey.com/product-detail/en/M2011S2A1W01/360-3240-ND/1049342/?itemSeq=302805119)
antenna pads | 1 |  | $0.00 | P1 |  |  | From Nvidia dev board |  | Antenna pads
4 Pin Connector | 1 | $0.21 | $0.21 | U$10 |  |  |  |  | 455-2249-ND‎ (https://www.digikey.com/product-detail/en/B4B-XH-A(LF)(SN)/455-2249-ND/1651047/?itemSeq=302805122)
Power LED | 1 | $0.58 | $0.58 | LED 1 |  | LED power indicator |  | Or any other 5mm LED, current around 20 mA | LED5MM
 |  | Total | $3468.72

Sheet: v2.0
Component | Quantity | Cost |  | Link | Order Status | Comment
Traxxas 1/10th Car platform with RC, NiMH battery 3000mAh, 7 cell and Charger | 1 | $299.95 | $299.95 | http://www.jegs.com/i/Traxxas/430/74054-6/10002/-1 | 0 | If out of stock, see alternate platforms below
USB wifi dongle |  | $8.99 | $0.00 | http://amzn.to/2nQGg3Z | 0 | use onboard WLAN or usb dongles like these instead of Ubiquity picostation ( product is discontinued)
Li-Po battery 5000mAh, 3 cell 11.1V #2872 | 1 | $74.99 | $74.99 | https://traxxas.com/products/parts/batteries/idpowercellbatteries/lipo/2872X-5000mah-111v-3S-25C | 0 | Combinations also available for purchase : https://www.amazon.com/dp/B01M0PKSGB https://www.amazon.com/Traxxas-Maxx-Brushless-BATTERY-CHARGER/dp/B00ERUAQYO
 |  |  |  | https://www.amazon.com/Traxxas-2831X-5000mAh-3-Cell-Battery/dp/B01A6YDKS8
Li-Po battery Charger #2970 | 1 | $49.99 | $49.99 | https://traxxas.com/products/parts/chargers/2970ezpeakplus4ampid https://www.amazon.com/Traxxas-2970-EZ-Peak-Charger-Identification/dp/B00OAFYLJC https://traxxas.com/products/parts/chargers/ezpeak-dual-8amp-id | 0
Nvidia Jetson TX1 | 1 | $299.00 | $299.00 | https://www.nvidia.com/en-us/autonomous-machines/embedded-systems-dev-kits-modules/ http://www.nvidia.com/object/edu-discount.html http://www.nvidia.com/object/jetsontx2-edu-discount.html | 0 | Avail Tx1/TX2 Development Kit through Academic discount Also, either of TX1 or TX2 can be used
Orbitty Carrier board for TX1 | 1 | $173.00 | $173.00 | http://connecttech.com/product/orbitty-carrier-for-nvidia-jetson-tx2-tx1/ | 0 | works for both TX1 or TX2
USB Hub | 1 | $29.95 | $29.95 | https://www.amazon.com/AmazonBasics-Port-USB-Power-Adapter/dp/B00DQFGH80 https://www.amazon.com/Sabrent-4-Port-Individual-Switches-HB-UM43/dp/B00JX1ZS5O | 0
FTDI | 1 | $15.00 | $15.00 | https://www.sparkfun.com/products/9873 | 0 | optional - depending on the IMU module
Sensors
SparkFun 9DoF Razor IMU M0 | 1 | $49.95 | $49.95 | https://www.sparkfun.com/products/14001 | 0
3DM Microstrain IMU (optional) |  |  |  | http://www.microstrain.com/inertial/3dm-gx3-25 |  | use either IMU
UM7 IMU (optional) |  |  |  | https://www.pololu.com/product/2740 http://www.chrobotics.com/shop/um7-orientation-sensor
LIDAR | 1 | $1775.00 | $1775.00 | https://acroname.com/products/HOKUYO-UST-10LX-LASER?sku=R359-UST-10LX | 0 | or scan-sweep lidar
Structure Sensor (Optional) | 1 | $379.00 | $379.00 | https://store.structure.io/store | 0 | or sviz - lidar and camera bundle
Asus xtion pro (optional) |  | - | - | https://www.amazon.com/Asus-Xtion-PRO-LIVE-90IW0122-B01UA/dp/B00CET0ZBO https://www.newegg.com/Product/Product.aspx?Item=N82E16826785030 |  | out of stock mostly
ZED Camera (Optional) |  | $449.00 | $0.00 | https://www.stereolabs.com/ | 0 | or rgb option
Mechanical
Traxxas 3769 Spring Preload Spacers | 2 | $5.22 | $10.44 | http://amzn.to/2aazUF7 | 0
Allen Key Set | 1 | $8.99 | $8.99 | http://amzn.to/29PazD5 | 0
Camera mount - 3d printed | 2 |  |  | - |  | 3d printed from files provided
Ubiquity Picostation mount - 3d printed ( optional) | 1 |  |  | - |  | 3d printed from files provided
plastic spacers /standoffs | 4 |  |  |  |  | between the carrier board and the TX1 mounting
3mm ABS | 1 | $6.38 | $6.38 | http://amzn.to/29E6CTy https://www.mcmaster.com/#8586k361/=1bnvvd6 | 0 | For Lidar mount of chassis
6mm ABS | 1 | $9.74 | $9.74 | http://amzn.to/29PayPj https://www.mcmaster.com/#8586k371/=1bnvv5e | 0 | For Base plate of chassis
6mm Hex M/F Standoff 14mm | 8 | 4.2 | $33.60 | https://www.mcmaster.com/#93655a425/=1bhcvt6
6mm Hex F/F Standoff 19mm | 6 | 2.79 | $16.74 | https://www.mcmaster.com/#92080a430/=1ak2153
6mm Hex F/F Standoff 45 mm | 4 | 2.8 | $11.20 | https://www.mcmaster.com/#92080a030/=1ak1644
6mm Hex F/F Standoff 35 mm | 4 | 2.53 | $10.12 | https://www.mcmaster.com/#92080a024/=1ak1tj1
M3 screws x 10 mm | 26 | 7.01 | $7.01 | https://www.mcmaster.com/#91290a115/=1bhcq40 |  | for a pack of 100
M3 screws x 20 mm | 6 | 6.85 | $6.85 | https://www.mcmaster.com/#91502a109/=1bhcs7r |  | for a pack of 50
Power Board
Refer to the Power Board BOM for specific components
Miscelleneous
Traxxas 2976 AC to DC Converter | 1 | $25.79 | $25.79 | http://amzn.to/29Fx5xq | 0
Micro USB Cable | 1 | $4.99 | $4.99 | http://amzn.to/29xNHFc | 0 | for teensy to usb hub
Ethernet cable (optional) | 1 | $2.99 | $2.99 | http://amzn.to/29xO2ry | 0 | for ubiquity (optional)
POE cable (optional) | 1 | $3.99 | $3.99 | http://amzn.to/29D7Lou | 0 | for ubiquity (optional)
Traxxas Lipo to JST balance cable extender | 1 | $14.99 | $14.99 | https://www.amazon.com/HobbyStar-Traxxas-Charge-Adapter-Adapters/dp/B076N68H4G https://www.amazon.com/dp/B071GS515J/ref=psdc_2234135011_t1_B075W3C42B
USB to Ethernet adapter ( for lidar with ethernet conn) | 1 | $9.49 | $9.49 | https://www.amazon.com/Cable-Matters-Ethernet-Network-Adapter/dp/B00ET4KHJ2
Servo cable | 1 | $3.00 | $3.00 | http://amzn.to/29xPaeq | 0 | ($3.06 per pack of 10)
4 AA batteries | 1 | $7.18 | $7.18 | http://amzn.to/29EIImY | 0 | for RC
SD Cards (optional) | 2 | $24.95 | $49.90 | http://amzn.to/29ItJe7 | 0
Bill of Material for Power Board v3.0
On 2/5/2019 at 11:41:38 AM
Comment | Quantity | Cost |  | Components |  | Comment | Order Link | Comments | Pattern
Power Board | 1 | 30 | 30 |  |  |  | https://oshpark.com/shared_projects/PM1kJ6E3
560 ohm | 1 |  | 0 | R1 |  | Resistor | https://www.digikey.com/product-detail/en/stackpole-electronics-inc/CF14JT560R/CF14JT560RTR-ND/1741466 | Any resistor around 500 ohm should work | AXIAL-0.4
0.33uF | 1 |  | 0 | C5 |  | CAPACITOR, American symbol | https://www.digikey.com/product-detail/en/tdk-corporation/FK16X7R2A334K/445-8365-ND/2815295 |  | C050-035X075
100nF | 3 |  | 0 | C6, C3, C4 |  | CAPACITOR, American symbol | https://www.digikey.com/product-detail/en/kemet/C328C102K3G5TA7301/C328C102K3G5TA7301-ND/6671502 |  | C050-035X075 | For a bag of capacitors (except the 0.33 u): | https://www.sparkfun.com/products/13698
100u | 2 |  | 0 | C1, C2 |  | CAPACITOR, American symbol | https://www.digikey.com/product-detail/en/panasonic-electronic-components/ECA-1HM101B/P10397TB-ND/268482 |  | C050-035X075
10uF | 1 |  | 0 | C7 |  | CAPACITOR, American symbol | https://www.digikey.com/product-detail/en/nichicon/UVR1H100MDD1TD/493-5915-1-ND/3438479 |  | C050-035X075
12V to 8V LDO | 1 | 0.92 | 0.92 | U1 |  | 12V to 8V LDO | https://www.digikey.com/product-detail/en/rohm-semiconductor/BA7808CP-E2/BA7808CP-E2CT-ND/2357332 |  | BA7808CP-E2
12V_TRANSFORMER | 1 | 34.94 | 34.94 | U$9 |  | CUI Inc ?? SERIES: PDQ30-D ?? DESCRIPTION: DC-DC CONVERTER http://www.mouser.com/pdfdocs/pdq30-d.pdf | https://www.digikey.com/product-detail/en/cui-inc/PDQ30-Q24-S12-D/102-3892-ND/6165425 |  | 12V_TRANSFORMER
22-23-2021 | 7 | 0.94 | 6.58 | X1, X2, X3, X4, X5, X6, X7 |  | .100 (2.54mm) Center Header - 2 Pin" | https://www.digikey.com/product-detail/en/on-shore-technology-inc./ostvn02a150/ed10561-nd/1588862 |  | 22-23-2021
360-3240-ND | 1 | 3.37 | 3.37 | U$3 |  | SPST two lead switch Pin 2 is common Swtich Closed on Down Position DigiKey: http://www.digikey.com/product-detail/en/nkk-switches/M2011S2A1W01/360-3240-ND/1049342 Data Sheet: http://2t70un3m1d9z1kztamkdrd38.wpengine.netdna-cdn.com/wp-content/uploads/2016/02/MtogglesBushing.pdf | https://www.digikey.com/product-detail/en/nkk-switches/M2011S2A1W01/360-3240-ND/1049342 |  | 360-3240-ND
antenna pads | 1 |  | 0 | P1 |  |  | From Nvidia dev board |  | Antenna pads
BATT | 1 | 0.21 | 0.21 | U$10 |  |  | https://www.digikey.com/products/en?keywords=b4b-xh-a(LF)(SN) |  | BATTERY_CONNECTOR
Power LED | 1 | 0.41 | 0.41 | LED 1 |  | LED power indicator | https://www.digikey.com/product-detail/en/lite-on-inc/LTL-4263/160-1964-ND/3198540 | Or any other 5mm LED, current around 20 mA | LED5MM | For a bag of 25 red LED | https://www.sparkfun.com/products/9856
 |  | Total | $3465.65

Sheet: v1.0
Component | Quantity | Cost |  | Link | Order Status | Comment
Traxxas 1/10th Car platform with RC, NiMH battery 3000mAh, 7 cell and Charger | 1 | $299.95 | $299.95 | http://www.jegs.com/i/Traxxas/430/74054-6/10002/-1 | 0 | If out of stock, see alternate platforms below
Ubiquity Picostation | 1 | $0.00 | $0.00 | http://amzn.to/29QPlq8 | 0 | Phased out of production. Use USB wifi dongles like one suggested below
Energizer Battery Pack | 1 | $159.00 | $159.00 | http://amzn.to/2aaBmHu | 0 | This replaces the older XP8000, which is no longer available
Nvidia Jetson TK1 | 1 | $192.99 | $192.99 | http://amzn.to/29EI3C2 | 0
USB Hub | 1 | $29.95 | $29.95 | http://amzn.to/29D7kKG | 0
FTDI | 1 | $15.00 | $15.00 | https://www.sparkfun.com/products/9873 | 0
Sensors
SparkFun 9DoF Razor IMU M0 | 1 | $49.95 | $49.95 | https://www.sparkfun.com/products/14001 | 0
LIDAR | 1 | $1775.00 | $1775.00 | https://acroname.com/products/HOKUYO-UST-10LX-LASER?sku=R359-UST-10LX | 0
Structure Sensor (Optional) | 1 | $379.00 | $379.00 | https://store.structure.io/store | 0
ZED Camera (Optional) | 1 | $449.00 | $449.00 | https://www.stereolabs.com/ | 0
Mechanical
Traxxas 3769 Spring Preload Spacers | 2 | $5.22 | $10.44 | http://amzn.to/2aazUF7 | 0
Allen Key Set | 1 | $8.99 | $8.99 | http://amzn.to/29PazD5 | 0
3mm ABS | 1 | $6.38 | $6.38 | http://amzn.to/29E6CTy | 0
6mm ABS | 1 | $9.74 | $9.74 | http://amzn.to/29PayPj | 0
M3 Hex nuts | 1 | $2.06 | $2.06 | http://www.mcmaster.com/#90591a250/=139rn2d | 0 | ($2.06 per pack of 100)
M3 Screw x 8mm | 1 | $6.58 | $6.58 | http://www.mcmaster.com/#91290A113 | 0 | ($6.58 per pack of 100)
M1.6 Screw x 8mm | 1 | $3.01 | $3.01 | http://www.mcmaster.com/#91290a041/=139r25l | 0 | ($3.01 per pack of 25)
M3 M-F Hex Standoff x 14mm | 12 | $1.57 | $18.84 | http://www.mcmaster.com/#98952a037/=139rm51 | 0
Power Board
Teensy 3.1 | 1 | $19.80 | $19.80 | https://www.pjrc.com/store/teensy32.html | 0
Miscelleneous
Traxxas 2976 AC to DC Converter | 1 | $25.79 | $25.79 | http://amzn.to/29Fx5xq | 0
Micro USB Cable | 1 | $4.99 | $4.99 | http://amzn.to/29xNHFc | 0
Mini USB Cable | 2 | $4.99 | $9.98 | https://www.amazon.com/Rerii-Length-Angle-cable-Charging/dp/B01E6MZBG0?s=wireless | 0
Ethernet cable | 1 | $2.99 | $2.99 | http://amzn.to/29xO2ry | 0
POE cable | 1 | $3.99 | $3.99 | http://amzn.to/29D7Lou | 0
Servo cable | 1 | $3.00 | $3.00 | http://amzn.to/29xPaeq | 0 | ($3.06 per pack of 10)
4 AA batteries | 1 | $7.18 | $7.18 | http://amzn.to/29EIImY | 0
Barrel Jack Connectors | 1 | $5.36 | $5.36 | http://amzn.to/29xOnKT | 0
M-M DC power coupler | 1 | $6.99 | $6.99 | http://amzn.to/2aaBvLn | 0
SD Cards | 2 | $24.95 | $49.90 | http://amzn.to/29ItJe7 | 0
 |  | Total | $3555.85

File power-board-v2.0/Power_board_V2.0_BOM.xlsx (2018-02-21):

S.No. | Designator | Description | Part No | Comment | Footprint | Quantity | Order link
1 | C1, C2 | 100uF polarized throughole capacitor |  | 100u | C050-035X075 | 2
2 | C3, C4, C6, C8, C9 | 100nF non-polarized throughole capacitor |  | 100n | C050-035X075 | 5
3 | C5 | 330nF non-polarized throughole capacitor |  | 0.33uF | C050-035X075 | 1
5 | C7 | 10uF polarized throughole capacitor |  | 10uF | C050-035X075 | 1
6 | CON1, CON2, CON3, CON4 | 3x1 0.1" male headers |  | 3 pin male header | MA03-1 | 4
7 | D2, D3, LED1 | Red colour throughole Led |  | Led | LED5MM | 3
8 | JP1 | 5x2 0.1" male headers |  | 2x5 male headers | 2X05 | 1
9 | P1 | Right angled Antenna bracket with screws and ufl to SMA cable along with Antennas |  | Antenna bracket | Antenna pads | 1 | Extract from Nvidia TX1 dev board | https://www.ebay.com/itm/ipx-u-fl-to-sma-Male-MHF4-MALE-FEMALE-Antenna-Extension-Cable-MINI-PCI-Card/192116656446
10 | R2, R3, R1 | 360 ohm throughole resistors |  | 360ohms | 0207/10 | 3
11 | SWITCH1, SWITCH2 | SWITCH SLIDE SPDT 100MA 12V | OS102011MS2QN1 | CKN9565-NDCKN9565-ND | CKN9565-ND | 2 | https://www.digikey.com/products/en?keywords=CKN9565-ND
12 | U1 | IC REG LINEAR 8V 1A TO220CP-3 | BA7808CP-E2 | 12V to 8V LDO | BA7808CP-E2 | 1 | https://www.digikey.com/product-detail/en/rohm-semiconductor/BA7808CP-E2/BA7808CP-E2CT-ND/2357332
13 | U$1 | Teensy 3.2 microcontroller with male pins |  | TEENSY-3.2 | TEENSY-3.2 | 1 | https://www.pjrc.com/store/teensy32_pins.html
14 | U$2 | 3S LiPo Protection PCB | Tenergy protection module | LIPO_PROTECTION | LIPO_PROTECTION | 1 | https://www.amazon.com/gp/product/B0021ZN8WY
15 | U$3, U$4, U$5 | SWITCH TOGGLE SPST 6A 125V | M2011S2A1W01 | 360-3240-ND | 360-3240-ND | 3 | https://www.digikey.com/product-detail/en/nkk-switches/M2011S2A1W01/360-3240-ND/1049342
16 | U$7 | CONN PWR JACK 1.7X4MM SOLDER | PJ-054 | 12 V connector for nvidia |  | 1 | https://www.digikey.com/product-detail/en/cui-inc/PJ-054/CP-054-ND/1644595 https://www.digikey.com/product-detail/en/cui-inc/PJ-018H-SMT-TR/CP-018HPJCT-ND/1530984
17 | U$9 | DC/DC CONVERTER 12V 30W | PDQ30-Q24-S12-D | 12V_TRANSFORMER | 12V_TRANSFORMER | 1 | https://www.digikey.com/product-detail/en/cui-inc/PDQ30-Q24-S12-D/102-3892-ND/6165425
18 | U$10 | CONN HEADER XH TOP 4POS 2.5MM | B4B-XH-A(LF)(SN) | BATT | BATTERY_CONNECTOR | 1 | https://www.digikey.com/products/en?keywords=b4b-xh-a(LF)(SN)
19 | X1, X2, X3, X4, X5, X6, X7, X8, X9 | CONN TERM BLOCK 2.54MM 2POS PCB | OSTVN02A150 | 22-23-2021 | 22-23-2021 | 9 | https://www.digikey.com/product-detail/en/on-shore-technology-inc./ostvn02a150/ed10561-nd/1588862
20 |  | 14x1 0.1" Female header (for Teensy on the PCB) |  |  |  | 2
21 |  | M3 screws x 10 mm |  | For mounting the Antenna Brackets |  | 2 | https://www.mcmaster.com/#91290a115/=1bhcq40
22 |  | 6mm Hex F/F Standoff 19mm |  |  |  | 2 | https://www.mcmaster.com/#92080a430/=1ak2153

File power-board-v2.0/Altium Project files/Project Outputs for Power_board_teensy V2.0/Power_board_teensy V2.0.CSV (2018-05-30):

Bill of Material for
On 1/31/2018 at 2:59:21 PM
Comment | Pattern | Quantity | Components
0.33uF | C050-035X075 | 1 | C5 | CAPACITOR, American symbol
1 | MA03-1 | 1 | CON1 | PIN HEADER
100n | C050-035X075 | 2 | C3, C4 | CAPACITOR, American symbol
100nF | C050-035X075 | 3 | C6, C8, C9 | CAPACITOR, American symbol
100u | C050-035X075 | 2 | C1, C2 | CAPACITOR, American symbol
10uF | C050-035X075 | 1 | C7 | CAPACITOR, American symbol
12 V | CP-054-ND | 1 | U$7 | DigiKey: http://www.digikey.com/product-detail/en/cui-inc/PJ-054/CP-054-ND/1644595 Data Sheet: http://www.cui.com/product/resource/pj-054.pdf
12V to 8V LDO | BA7808CP-E2 | 1 | U1 | 12V to 8V LDO
12V_TRANSFORMER | 12V_TRANSFORMER | 1 | U$9 | CUI Inc ¦ SERIES: PDQ30-D ¦ DESCRIPTION: DC-DC CONVERTER http://www.mouser.com/pdfdocs/pdq30-d.pdf
2.2v 20mA | LED5MM | 1 | LED1 | LED OSRAM: - CHIPLED LG R971, LG N971, LY N971, LG Q971, LY Q971, LO R971, LY R971 LH N974, LH R974 LS Q976, LO Q976, LY Q976 LO Q996 - Hyper CHIPLED LW Q18S LB Q993, LB Q99A, LB R99A - SideLED LS A670, LO A670, LY A670, LG A670, LP A670 LB A673, LV A673, LT A673, LW A673 LH A674 LY A675 LS A676, LA A676, LO A676, LY A676, LW A676 LS A679, LY A679, LG A679 - Hyper Micro SIDELED® LS Y876, LA Y876, LO Y876, LY Y876 LT Y87S - SmartLED LW L88C, LW L88S LB L89C, LB L89S, LG L890 LS L89K, LO L89K, LY L89K LS L896, LA L896, LO L896, LY L896 - TOPLED LS T670, LO T670, LY T670, LG T670, LP T670 LSG T670, LSP T670, LSY T670, LOP T670, LYG T670 LG T671, LOG T671, LSG T671 LB T673, LV T673, LT T673, LW T673 LH T674 LS T676, LA T676, LO T676, LY T676, LB T676, LH T676, LSB T676, LW T676 LB T67C, LV T67C, LT T67C, LS T67K, LO T67K, LY T67K, LW E67C LS E67B, LA E67B, LO E67B, LY E67B, LB E67C, LV E67C, LT E67C LW T67C LS T679, LY T679, LG T679 LS T770, LO T770, LY T770, LG T770, LP T770 LB T773, LV T773, LT T773, LW T773 LH T774 LS E675, LA E675, LY E675, LS T675 LS T776, LA T776, LO T776, LY T776, LB T776 LHGB T686 LT T68C, LB T68C - Hyper Mini TOPLED® LB M676 - Mini TOPLED Santana® LG M470 LS M47K, LO M47K, LY M47K Source: http://www.osram.convergy.de LUXEON: - LUMILED® LXK2-PW12-R00, LXK2-PW12-S00, LXK2-PW14-U00, LXK2-PW14-V00 LXK2-PM12-R00, LXK2-PM12-S00, LXK2-PM14-U00 LXK2-PE12-Q00, LXK2-PE12-R00, LXK2-PE12-S00, LXK2-PE14-T00, LXK2-PE14-U00 LXK2-PB12-K00, LXK2-PB12-L00, LXK2-PB12-M00, LXK2-PB14-N00, LXK2-PB14-P00, 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
2 | MA03-1 | 1 | CON2 | PIN HEADER
22-23-2021 | 22-23-2021 | 9 | X1, X2, X3, X4, X5, X6, X7, X8, X9 | .100 (2.54mm) Center Header - 2 Pin"
3.3v 10mA | LED5MM | 2 | D2, D3 | LED OSRAM: - CHIPLED LG R971, LG N971, LY N971, LG Q971, LY Q971, LO R971, LY R971 LH N974, LH R974 LS Q976, LO Q976, LY Q976 LO Q996 - Hyper CHIPLED LW Q18S LB Q993, LB Q99A, LB R99A - SideLED LS A670, LO A670, LY A670, LG A670, LP A670 LB A673, LV A673, LT A673, LW A673 LH A674 LY A675 LS A676, LA A676, LO A676, LY A676, LW A676 LS A679, LY A679, LG A679 - Hyper Micro SIDELED® LS Y876, LA Y876, LO Y876, LY Y876 LT Y87S - SmartLED LW L88C, LW L88S LB L89C, LB L89S, LG L890 LS L89K, LO L89K, LY L89K LS L896, LA L896, LO L896, LY L896 - TOPLED LS T670, LO T670, LY T670, LG T670, LP T670 LSG T670, LSP T670, LSY T670, LOP T670, LYG T670 LG T671, LOG T671, LSG T671 LB T673, LV T673, LT T673, LW T673 LH T674 LS T676, LA T676, LO T676, LY T676, LB T676, LH T676, LSB T676, LW T676 LB T67C, LV T67C, LT T67C, LS T67K, LO T67K, LY T67K, LW E67C LS E67B, LA E67B, LO E67B, LY E67B, LB E67C, LV E67C, LT E67C LW T67C LS T679, LY T679, LG T679 LS T770, LO T770, LY T770, LG T770, LP T770 LB T773, LV T773, LT T773, LW T773 LH T774 LS E675, LA E675, LY E675, LS T675 LS T776, LA T776, LO T776, LY T776, LB T776 LHGB T686 LT T68C, LB T68C - Hyper Mini TOPLED® LB M676 - Mini TOPLED Santana® LG M470 LS M47K, LO M47K, LY M47K Source: http://www.osram.convergy.de LUXEON: - LUMILED® LXK2-PW12-R00, LXK2-PW12-S00, LXK2-PW14-U00, LXK2-PW14-V00 LXK2-PM12-R00, LXK2-PM12-S00, LXK2-PM14-U00 LXK2-PE12-Q00, LXK2-PE12-R00, LXK2-PE12-S00, LXK2-PE14-T00, LXK2-PE14-U00 LXK2-PB12-K00, LXK2-PB12-L00, LXK2-PB12-M00, LXK2-PB14-N00, LXK2-PB14-P00, 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
3 | MA03-1 | 1 | CON3 | PIN HEADER
360-3240-ND | 360-3240-ND | 3 | U$3, U$4, U$5 | SPST two lead switch Pin 2 is common Swtich Closed on Down Position DigiKey: http://www.digikey.com/product-detail/en/nkk-switches/M2011S2A1W01/360-3240-ND/1049342 Data Sheet: http://2t70un3m1d9z1kztamkdrd38.wpengine.netdna-cdn.com/wp-content/uploads/2016/02/MtogglesBushing.pdf
360ohms | 0207/10 | 2 | R2, R3 | RESISTOR, European symbol
4 | MA03-1 | 1 | CON4 | PIN HEADER
70ohms | 0207/10 | 1 | R1 | RESISTOR, European symbol
AGND |  | 1 | AGND2 | SUPPLY SYMBOL
antenna pads | Antenna pads | 1 | P1
BATT | BATTERY_CONNECTOR | 1 | U$10
CKN9565-NDCKN9565-ND | CKN9565-ND | 2 | SWITCH1, SWITCH2
GND_12 |  | 2 | AGND1, AGND3 | SUPPLY SYMBOL
LIPO_PROTECTION | LIPO_PROTECTION | 1 | U$2
PINHD-2X5 | 2X05 | 1 | JP1 | PIN HEADER
TEENSY-3.2 | TEENSY-3.2 | 1 | U$1 | 0.1 pin spacing"
V11.2 |  | 1 | V1 | SUPPLY SYMBOL
V12 |  | 7 | VDD1, VDD5, VDD6, VDD7, VDD8, VDD9, VDD10 | SUPPLY SYMBOL
V8 |  | 3 | VDD2, VDD3, VDD4 | SUPPLY SYMBOL

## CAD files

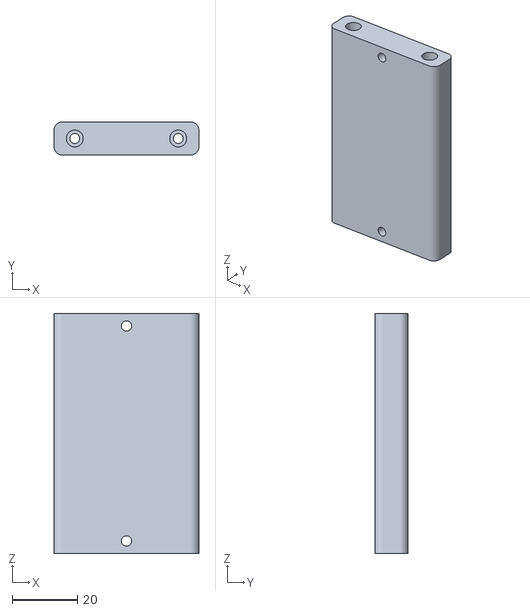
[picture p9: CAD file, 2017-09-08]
chassis/3dPrints/WifiMount.STL
44.5 x 10.2 x 73.7

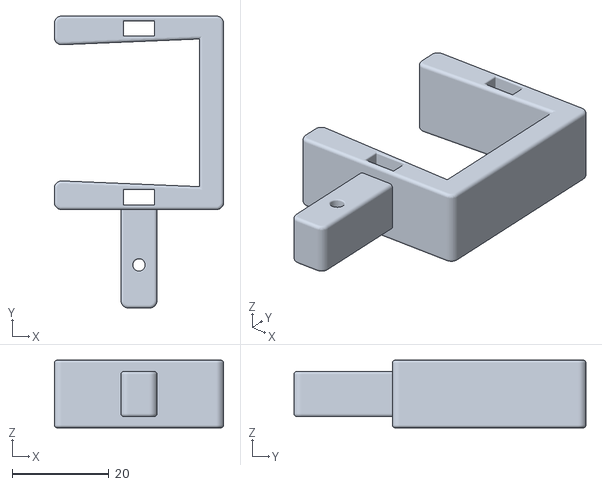
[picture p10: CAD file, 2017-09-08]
chassis/3dPrints/ZedMount2.STL
35.0 x 60.3 x 14.0

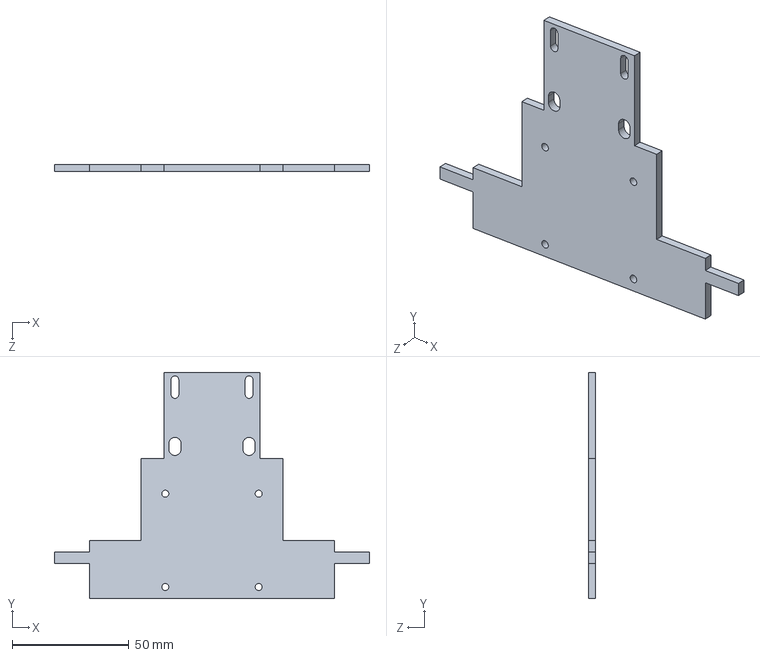
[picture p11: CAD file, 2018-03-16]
chassis/Lidar_Mount_10LX.SLDPRT
135.0 x 97.0 x 3.17 mm

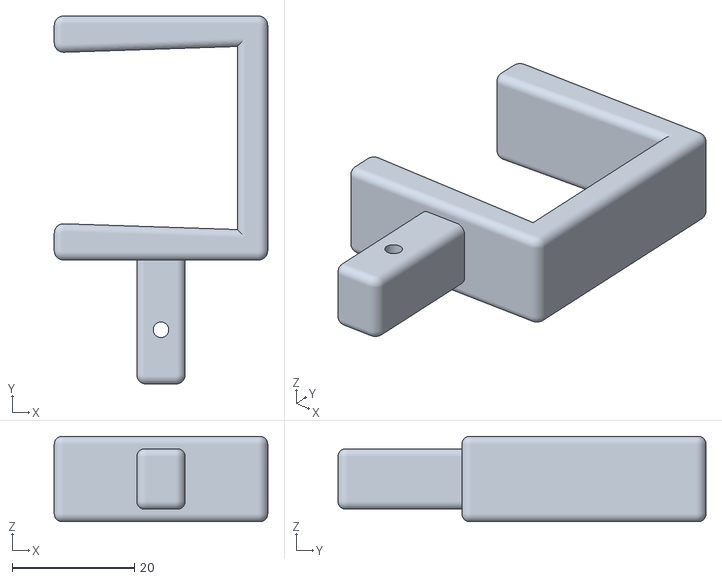
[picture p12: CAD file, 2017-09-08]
chassis/3dPrints/ZedMount.STL
35.0 x 60.3 x 14.0

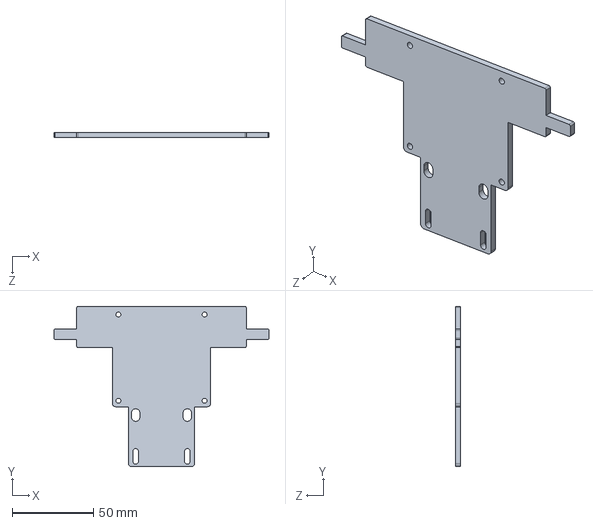
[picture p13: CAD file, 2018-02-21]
chassis/Lidar_Mount_30LX.SLDPRT
132.1 x 98.6 x 3.17 mm

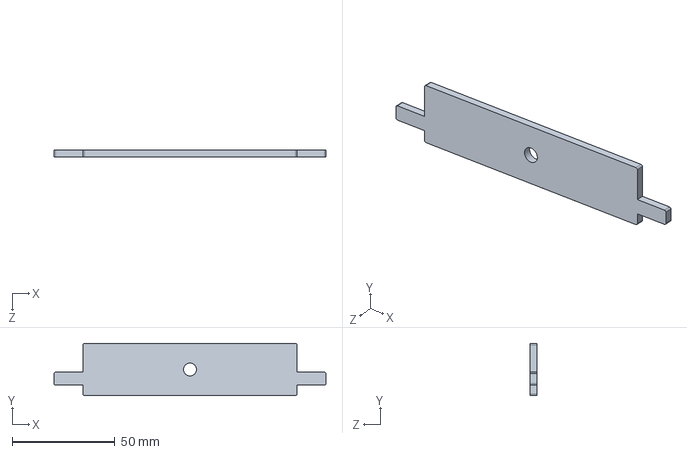
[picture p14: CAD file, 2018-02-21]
chassis/Camera_Base_Mount.SLDPRT
132.1 x 25.4 x 3.17 mm

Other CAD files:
chassis/Chassis_Surfaced_MASTER_small_powerboard.DWG
chassis/Chassis_Surfaced_MASTER.DWG
chassis/Camera_Mount.SLDPRT
chassis/Camera_Mount.STL
chassis/Lidar_Mount_10LX.DWG
chassis/Lidar_Mount_10LX.STL
chassis/Lidar_Mount_30LX.DWG

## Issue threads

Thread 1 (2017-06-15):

Do we need to connect pin 14 and 15 on the teensy?

AlickCameron, 2017-06-15:

slivingston, 2017-06-25:
I have not built one of the cars yet, but from my knowledge of schematics, pins 14 and 15 do not need to be connected anywhere. The labels SIG1 and SIG2 on pin 14 and pin 15 in the schematic may be errors.

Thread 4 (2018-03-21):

Typo in the Teensy Firmware README.md ?

MTDzi, 2018-03-21:
In the last step of the 3) point it reads:

`rosrun rosserial-arduino make_libraries.py .`

but that didn't work for. What instead did was:
`rosrun rosserial_arduino make_libraries.py .`

Is it just my version of ROS, or is this indeed a typo?
And if it is indeed a typo, would you like a PR, or would you like to fix it yourself?

MTDzi, 2018-07-25:
I created a Pull Request for that: #5

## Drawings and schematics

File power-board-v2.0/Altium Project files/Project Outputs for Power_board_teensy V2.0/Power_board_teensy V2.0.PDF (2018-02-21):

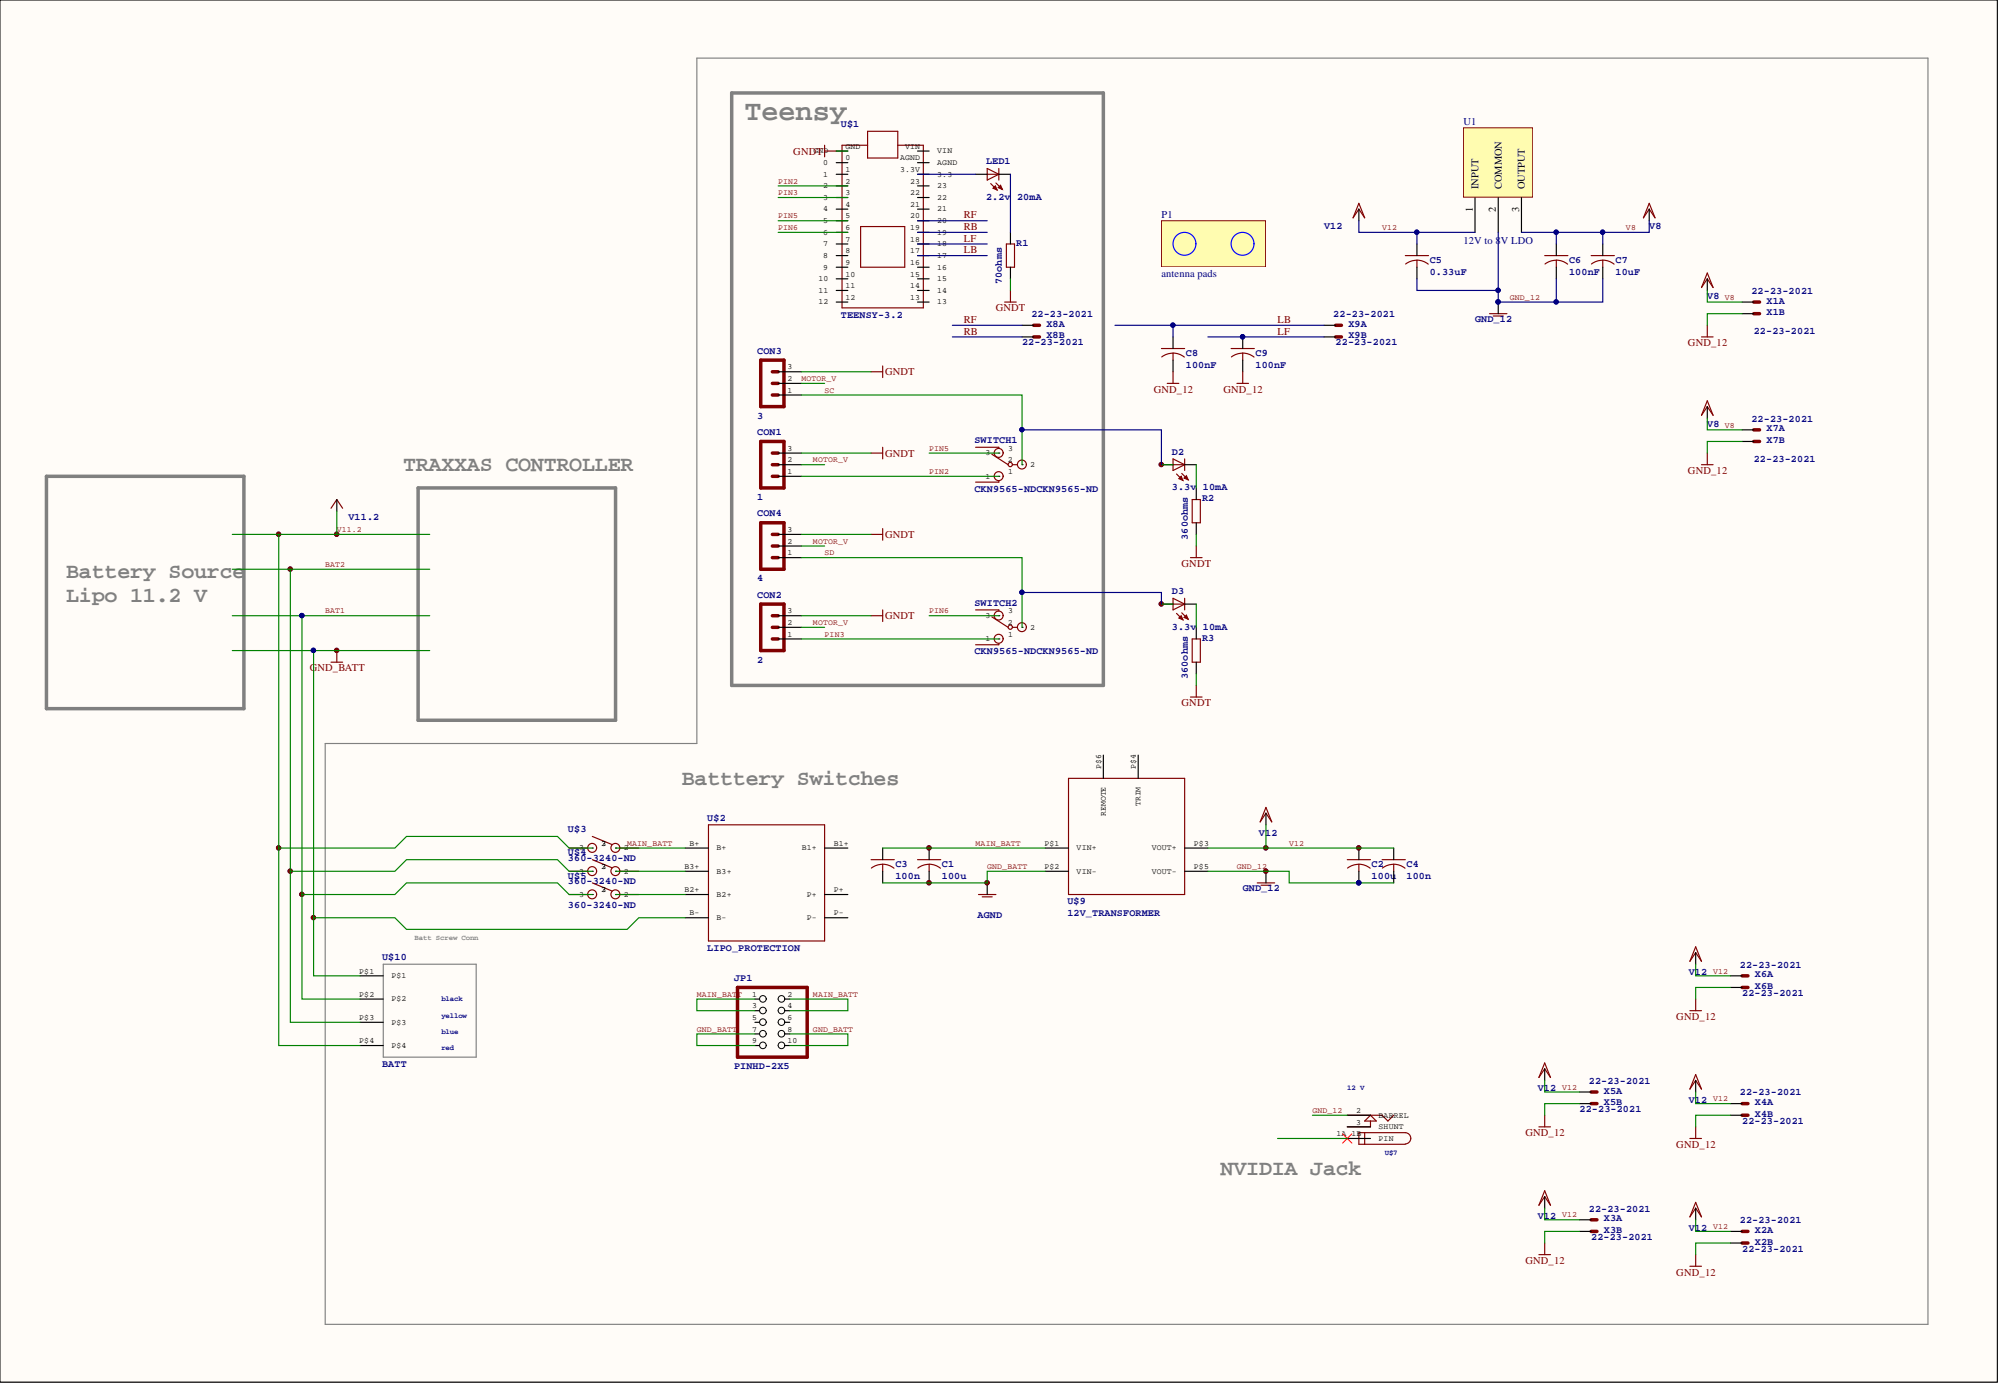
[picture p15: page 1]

GND_12

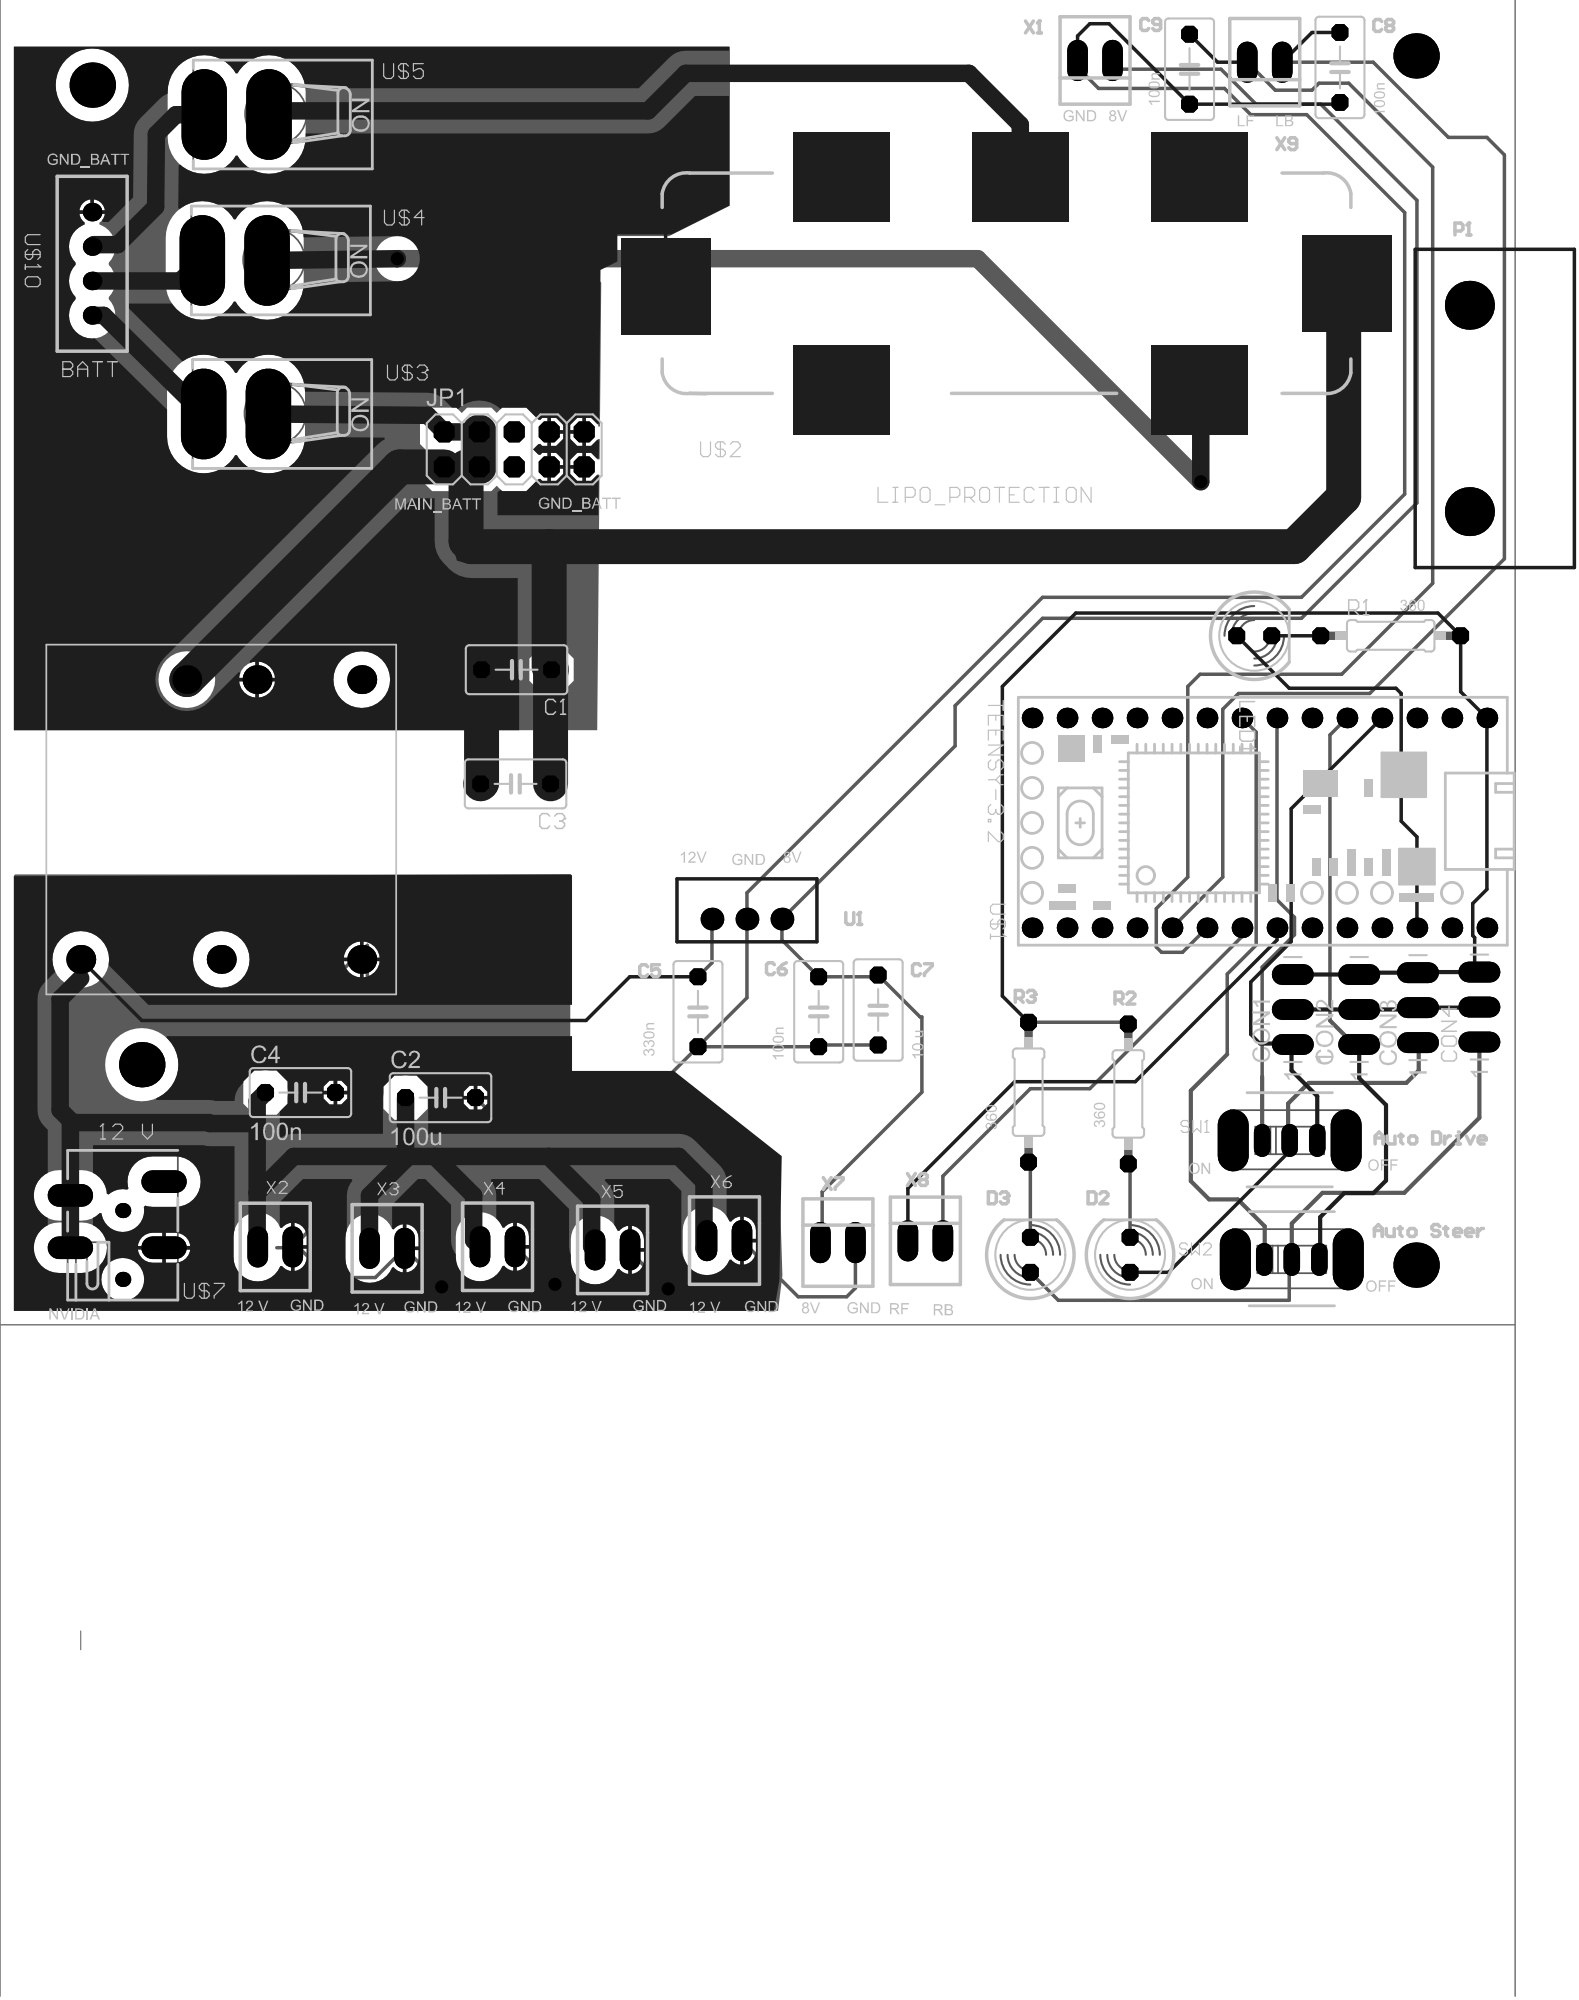
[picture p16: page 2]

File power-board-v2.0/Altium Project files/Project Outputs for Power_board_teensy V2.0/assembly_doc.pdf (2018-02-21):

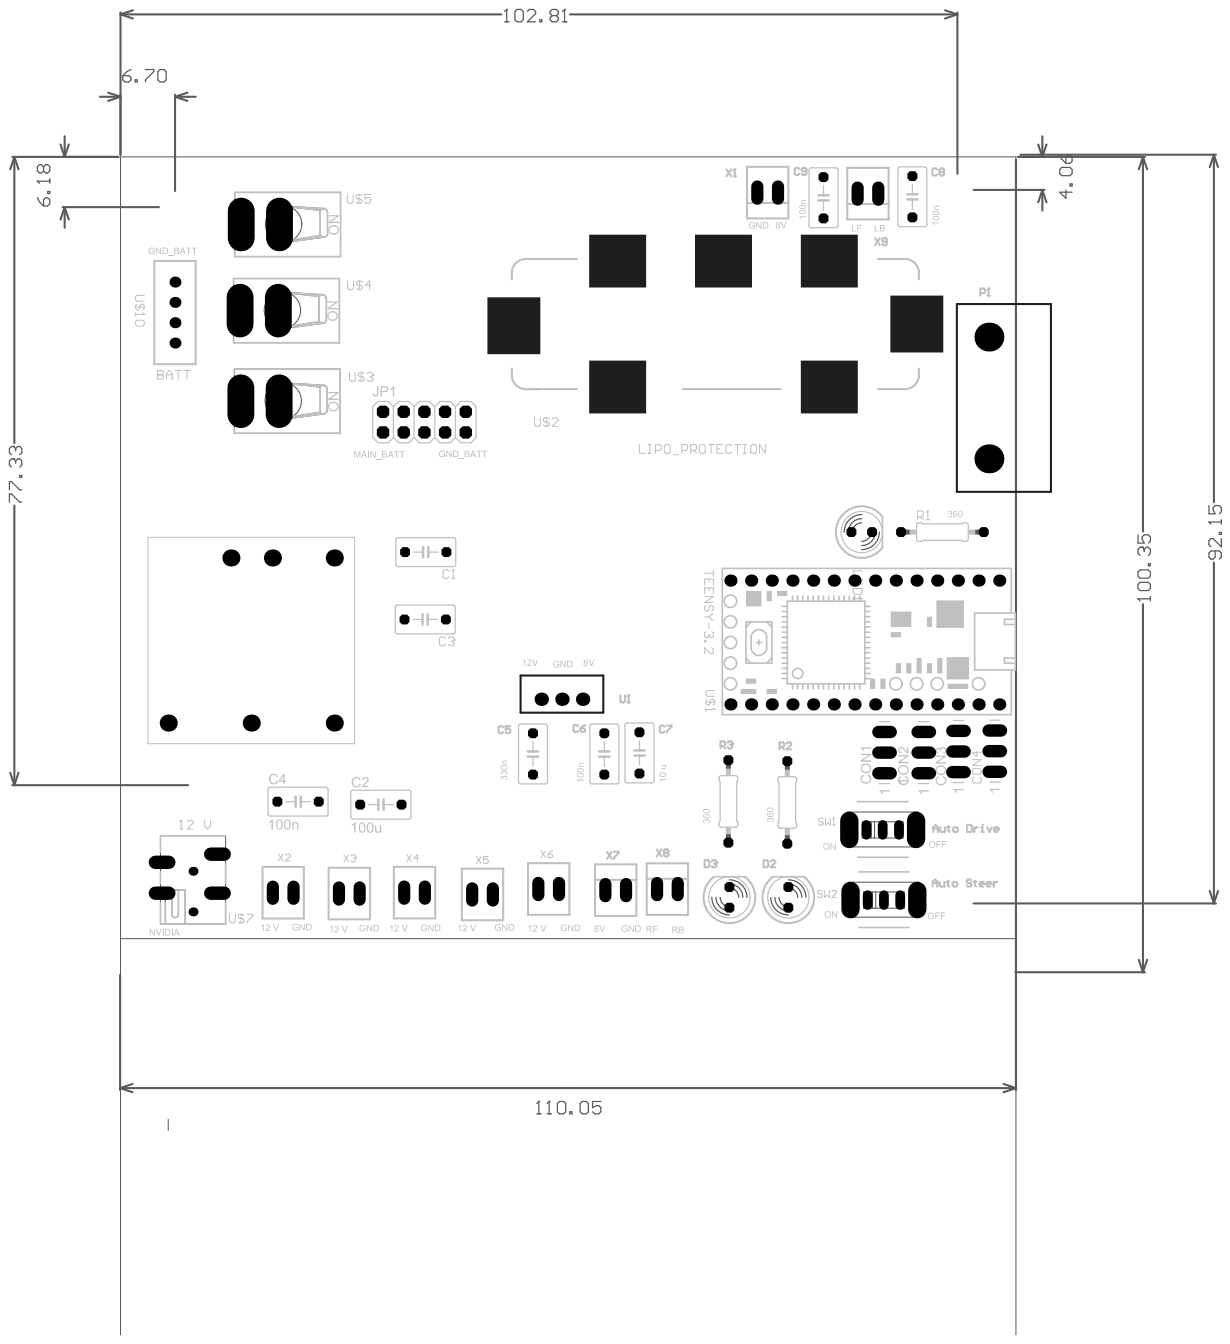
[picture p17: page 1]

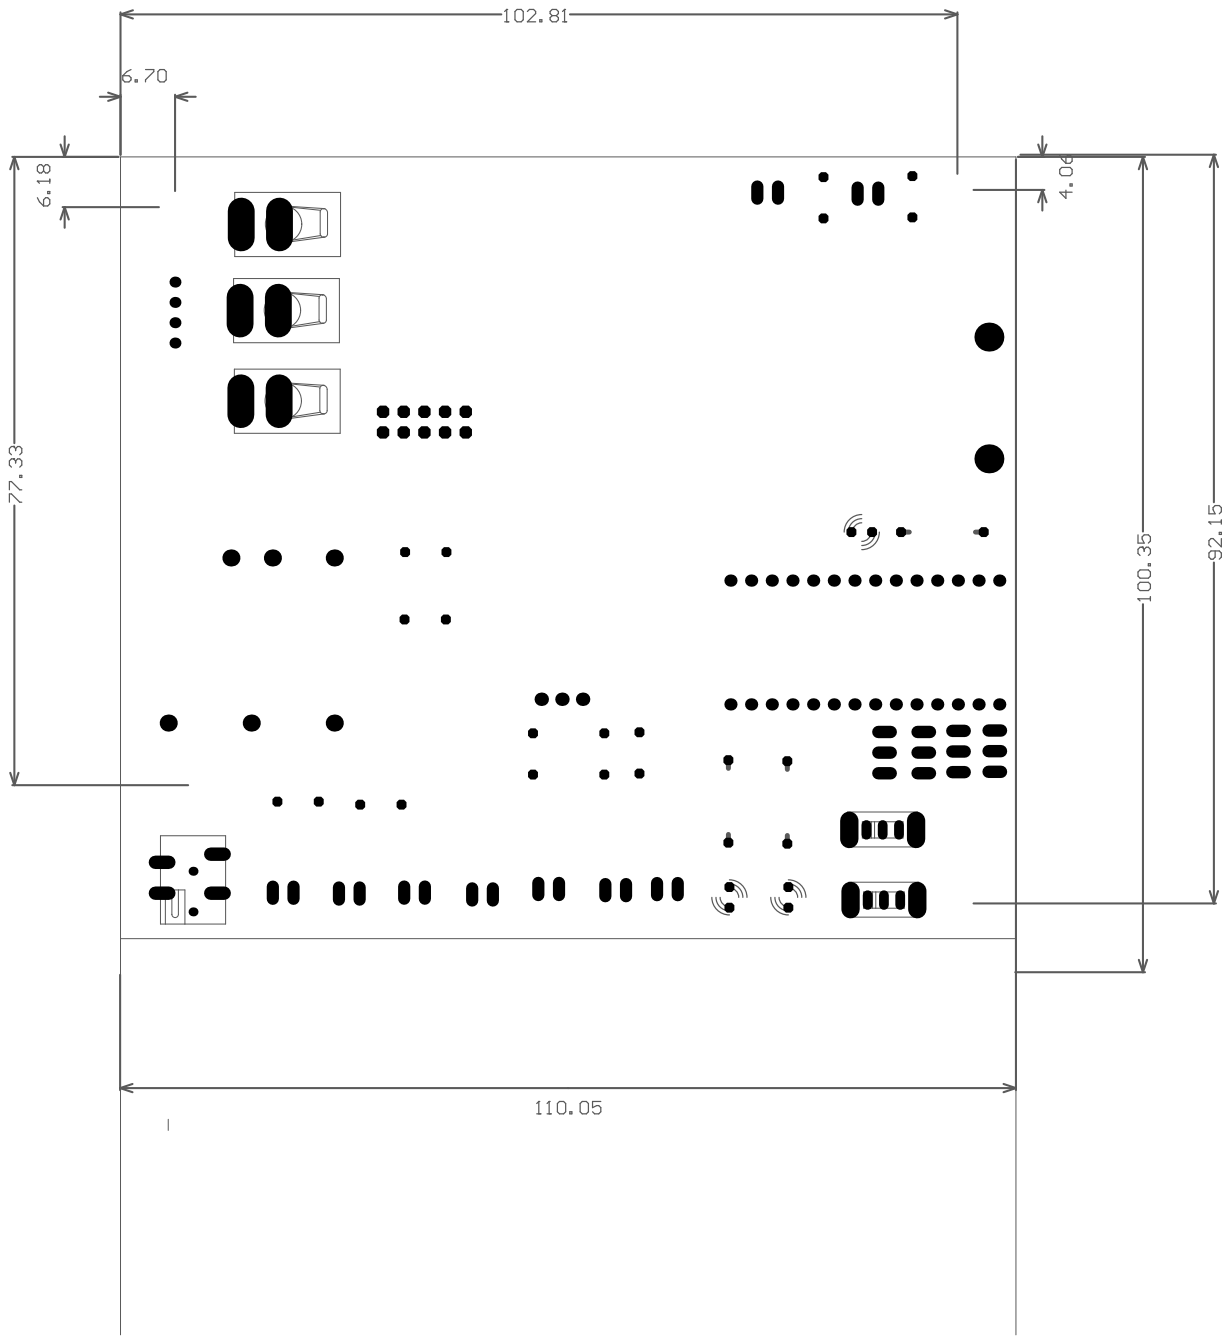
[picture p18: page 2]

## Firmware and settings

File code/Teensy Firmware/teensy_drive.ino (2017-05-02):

#include <ros.h>                // header files sourced from  Step 3
#include <std_msgs/Bool.h>      
#include <std_msgs/String.h>
#include <std_msgs/Int32.h>
#include <std_msgs/Empty.h>
#include <race/drive_values.h>
ros::NodeHandle  nh;


boolean flagStop = false;     // These values were cacluated for the specific Teensy microcontroller using an oscilloscope. 
int pwm_center_value = 9830;  //  15% duty cycle - corresponds to zero velocity, zero steering
int pwm_lowerlimit = 6554;    //  10% duty cycle - corresponds to max reverse velocity, extreme left steering
int pwm_upperlimit = 13108;   //  20% duty cycle - corresponds to max forward velocity, extreme right steering

std_msgs::Int32 str_msg;          // creater a ROS Publisher called chatter of type str_msg
ros::Publisher chatter("chatter", &str_msg);

int kill_pin = 2;     // This is the GPIO pin for emergency stopping.
unsigned long duration = 0;

void messageDrive( const race::drive_values& pwm ) 
{
//  Serial.print("Pwm drive : ");
//  Serial.println(pwm.pwm_drive);
//  Serial.print("Pwm angle : ");
//  Serial.println(pwm.pwm_angle);
  
  if(flagStop == false)
  {
    str_msg.data = pwm.pwm_drive;
    chatter.publish( &str_msg );

    if(pwm.pwm_drive < pwm_lowerlimit)  // Pin 5 is connected to the ESC..dive motor
    {
      analogWrite(5,pwm_lowerlimit);    //  Safety lower limit        
    }
    else if(pwm.pwm_drive > pwm_upperlimit)
    {
      analogWrite(5,pwm_upperlimit);    //  Safety upper limit
    }
    else
    {
      analogWrite(5,pwm.pwm_drive);     //  Incoming data                    
    }

    
    if(pwm.pwm_angle < pwm_lowerlimit) // Pin 6 is connected to the steering servo.
    {
      analogWrite(6,pwm_lowerlimit);    //  Safety lower limit        
    }
    else if(pwm.pwm_angle > pwm_upperlimit)
    {
      analogWrite(6,pwm_upperlimit);    //  Safety upper limit
    }
    else
    {
      analogWrite(6,pwm.pwm_angle);     //  Incoming data                    
    }

  }
  else
  {
    analogWrite(5,pwm_center_value);
    analogWrite(6,pwm_center_value);    
  }
}

void messageEmergencyStop( const std_msgs::Bool& flag )
{
  flagStop = flag.data;
  if(flagStop == true)
  {
    analogWrite(5,pwm_center_value);
    analogWrite(6,pwm_center_value);    
  }
}


ros::Subscriber<race::drive_values> sub_drive("drive_pwm", &messageDrive );   // Subscribe to drive_pwm topic sent by Jetson
ros::Subscriber<std_msgs::Bool> sub_stop("eStop", &messageEmergencyStop );  // Subscribe to estop topic sent by Jetson


void setup() {
  // Need to produce PWM signals so we need to setup the PWM registers. This setup happens next.
  analogWriteFrequency(5, 100); //  freq at which PWM signals is generated at pin 5.
  analogWriteFrequency(6, 100); 
  analogWriteResolution(16); // Resolution for the PWM signal
  analogWrite(5,pwm_center_value); // Setup zero velocity and steering.
  analogWrite(6,pwm_center_value);
  pinMode(13,OUTPUT); // Teensy's onboard LED pin. 
  digitalWrite(13,HIGH); // Setup LED.
  pinMode(kill_pin,INPUT); // Set emergency pin to accept inputs.
//  digitalWrite(2,LOW);

  nh.initNode();  // intialize ROS node
  nh.subscribe(sub_drive); // start the subscribers.
  nh.subscribe(sub_stop);

  nh.advertise(chatter);  // start the publisher..can be used for debugging.
}

void loop() {
  nh.spinOnce();
  duration = pulseIn(kill_pin, HIGH, 30000);  // continuously monitor the kill pin.
  while(duration > 1900) // stop if kill pin activated..setup everything to zero. 
  {
    duration = pulseIn(kill_pin, HIGH, 30000);
    analogWrite(5,pwm_center_value);
    analogWrite(6,pwm_center_value);        
  }
  // put your main code here, to run repeatedly:
  /*
  if(Serial.available())
  {
    int spd = Serial.read();
    if(spd>127) {
      spd = spd-128;
      spd = map(spd,0,100,410,820);
      analogWrite(5,spd);  
    }
    else {
      //angle servo
      spd = map(spd,0,100,410,820);
      analogWrite(6,spd);
    }
    
  } 
  */ 
}

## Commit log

2016-08-04 added laser cutting images
2016-08-05 added laser cutting dwgs and made laser cutting folder to hold both relevant folders
    [Big-Lidar_mount.DWG, HubBacker_label.DWG, IMU_Mount_v1.DWG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]
2017-09-08 Version 2.0 PCB and CAD files
    [Chassis_Surfaced_MASTER.DWG, Chassis_Surfaced_MASTER_holes.DWG, Main BOM.xlsx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]
2017-09-08 Power board image
2018-02-21 updated files for 2018 version
    [Camera_Base_Mount.SLDPRT, Camera_Mount.SLDPRT, Chassis_Surfaced_MASTER.DWG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]
2018-02-21 update repository
    [Big-Lidar_mount.DWG, Chassis_Surfaced_MASTER.DWG, Chassis_Surfaced_MASTER_holes.DWG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]
2018-02-28 Updated few links
    [F1tenth BOM 2018.xlsx]
2018-03-09 Updated README for 'Teensy Firmware'.
2018-03-16 updated Lidar mount
    [Lidar_Mount_10LX.DWG, Lidar_Mount_10LX.SLDPRT, Lidar_Mount_10LX.STL]
2018-07-25 Fixed typo in code/Teensy Firmware/README.txt
2019-03-03 Update BOM
    [F1tenth BOM 2019.xlsx]
2019-03-03 Update Chassis laser cut for power board v3
    [Chassis_Surfaced_MASTER_small_powerboard.DWG]
2019-03-03 Upload power-board-v3
2019-03-15 Added camera mount stl
    [Camera_Mount.STL]
2019-09-05 Add files via upload
    Updated power board BOM.
    [F1tenth BOM 2019.xlsx]
2020-03-03 Removed digikey cart link.
    [F1tenth BOM 2019.xlsx]
